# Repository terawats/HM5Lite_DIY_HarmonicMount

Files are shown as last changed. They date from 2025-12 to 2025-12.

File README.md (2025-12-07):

# HM5Lite DIY Harmonic Mount

## Introduction
  HM5 Lite is a DIY telescope tracker mount with a harmonic drive (gear). The mount weighs just 2.5 kg and supports a maximum payload capacity of 4–5 kg.
By leveraging the harmonic drive, which is strong enough to operate without the need for an additional counterweight, it offers several advantages.
It's convenient to carry and easy and quick to set up in a short time without weight balancing required.
  Software on this project are custom form [OnStepX](https://github.com/hjd1964/OnStepX) release v10.24c to support to keep telescope position on EEPROM.
EEPROM's used on this project are AT24C32 on "DS3231 AT24C32 I2C RTC module". 

## 💰 Cost and Usage
This project aims to minimize the material cost to under $180 USD.
It's affordable and easy to build (DIY) yourself. The target usage is for telescopes with a focal length not over 250 mm.
It's suitable for wide-angle photography such as the Milky Way and comets, and it's also good for deep-sky objects (DSOs).

## 🔭 Performance
With this configuration, we can achieve an RMS guiding error of 1.0" to 1.8" (arcseconds).
This is good enough for a telescope setup with a pixel scale of 3.0"–5.0"/pixel.

Examples:
RedCat51 + ASI2600MC Pro is 3.1"/pixel.
Samyang 135mm + ASI2600MC Pro is 5.7"/pixel. (Note: Changed "123mm" to the more common "135mm" focal length.)

Under these conditions, the guide error is not over 1/2 the pixel scale.

# Demo of performance



### See Demo Video on YouTube by click below image
Watch the demo (https://www.youtube.com/watch?v=0rcDmX7sShg)

### Auto guide test condition with platload 3kg


### See Auto Guide test result on YouTube by click below image
Watch the demo (https://youtu.be/mmUjZQFmkEI)

# Lists of component and Estimated cost
Below is a lists of component and estimated cost. Mosly cost are form Taobao.com and Aliexpress.com
| Items | Pictues | Desc | Q'ty  | cost |
|---|---|---|---|---|
| 1. Harmonic gear |  | miniF11-100 | x2 | 37 usd  |
| 2. Steping Motor |  | NEMA17 42x60mm | x2 | 5 usd  |
| 3. Close loop servo driver |  | SERVO42(step tick) | x2 | 8 usd  |
| 4. NEMA17 Motor L-bracket |  | 42mm L-Bracket | x2 | 1 usd  |
| 5. Latitude Adjusment wedge |  | 15kg load capacity | x1 | 23 usd  |
| 6. Dovetail clamp |  | Clamp for telescope | x1 | 6 usd  |
| 7. Wemos D1 mini ESP32 |  | OnStepX MCU | x1 | 3.5 usd  |
| 8. Wemos D1 mini Buzzer shield |  | OnStepX Buzzer | x1 | 1 usd  |
| 9. Wemos D1 mini Power shield |  | for ESP32 power | x1 | 1 usd  |
| 10. DS3231 AT24C32 I2C RTC module |  | for OnStep RTC | x1 | 2 usd  |
| 11. Female USB Type-C socket |  | for connect to PC | x1 | 1 usd  |
| 12. Female 2.5mm DC socket |  | for 12V power supply | x1 | 1 usd  |
| 13. 3D print parts for OnStepX | OnStep | file: Box_OnStepX.stl | - | 5 usd  |
| 14. 3D print parts for RA cable | DecCable | file: Box_RA_Cable_v2.stl | - | 3 usd  |
| 15. Cable management tube | IMG_flex | for RA wiring banagement  | - | 1 usd  |
| 16. Screw, Nute, washer | ImgScrew | for assembly | - | 8 usd  |
| Total estimation cost: | | | | 158 usd  |

# Schemetic daiagram

schemetic

# Assembly photo gallery
























### Custom OnStepX for HM5Lite 
Custom OnStepX version v10.24c and config for HM5Lite [download link](https://github.com/terawats/HM5Lite_DIY_HarmonicMount/releases)
Plaese download file name "Custom_OnStepX_for_HM5Lite.zip"

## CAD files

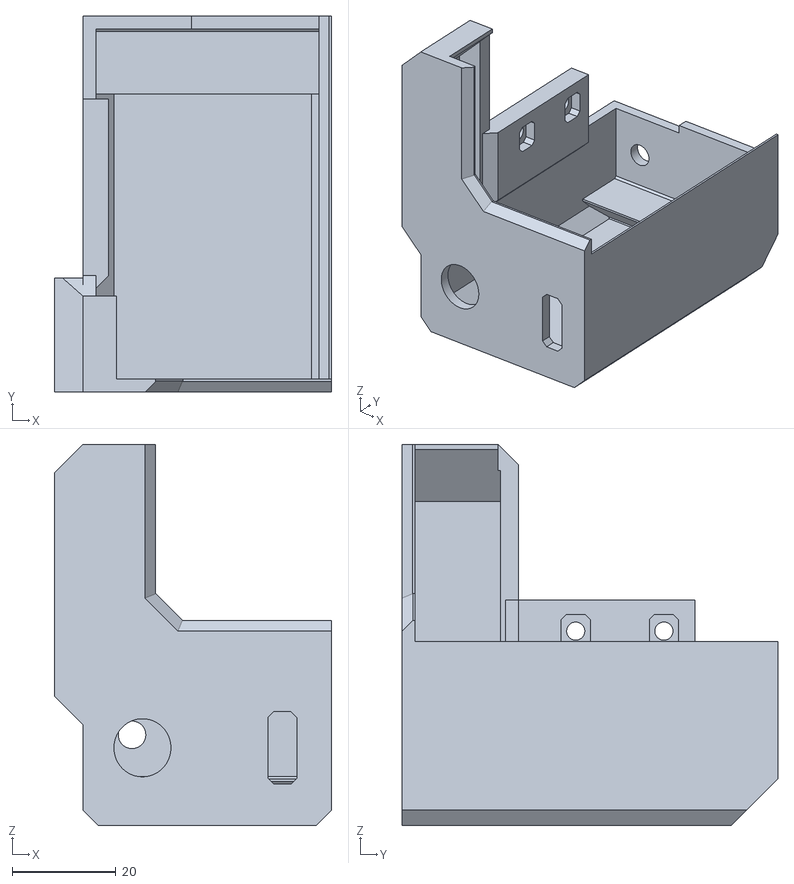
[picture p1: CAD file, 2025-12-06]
Box_OnStepX.stl
53.5 x 72.5 x 73.5

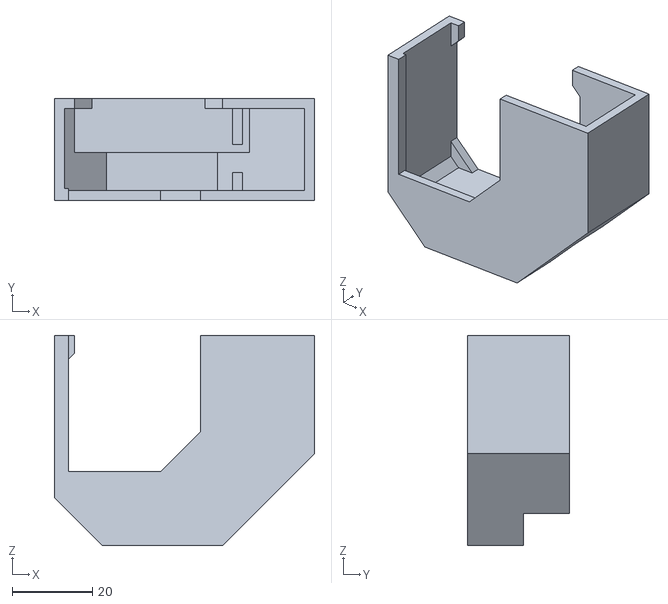
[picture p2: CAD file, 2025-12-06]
Box_RA_Cable_v2.stl
65.0 x 25.5 x 52.5

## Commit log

2025-12-06 OnStepX PCB housing box
    Box for install OnStepX PCB assembly
    [Box_OnStepX.stl, Box_RA_Cable_v2.stl]
2025-12-06 Box for RA cable management
    Box for RA cable management for better looks
2025-12-06 Box for RA cable management
    Box for RA cable management for better look
2025-12-06 Box for RA axis motor cable management
    Box for RA axis motor cable management for better look
    [Box_RA_Cable_v2.stl]
2025-12-07 Update README.md
    Add schematic diagram
